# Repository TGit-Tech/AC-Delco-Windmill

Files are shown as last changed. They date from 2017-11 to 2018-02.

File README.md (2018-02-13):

# AC-Delco Alternator Windmill
An AC Delco alternator Windmill for wind power generation

Release 2017.12.10-beta ( Pictures Below )
*INCOMPLETE PROJECT - Use for experimental only*
Tested in 40mph winds found that gear slippage and destruction occurs
Need to Refactor the design for more stability
However, Project has demonstrated the ability to charge @ ~ 20mph winds
This includes self-excitement ( Actual power gained )

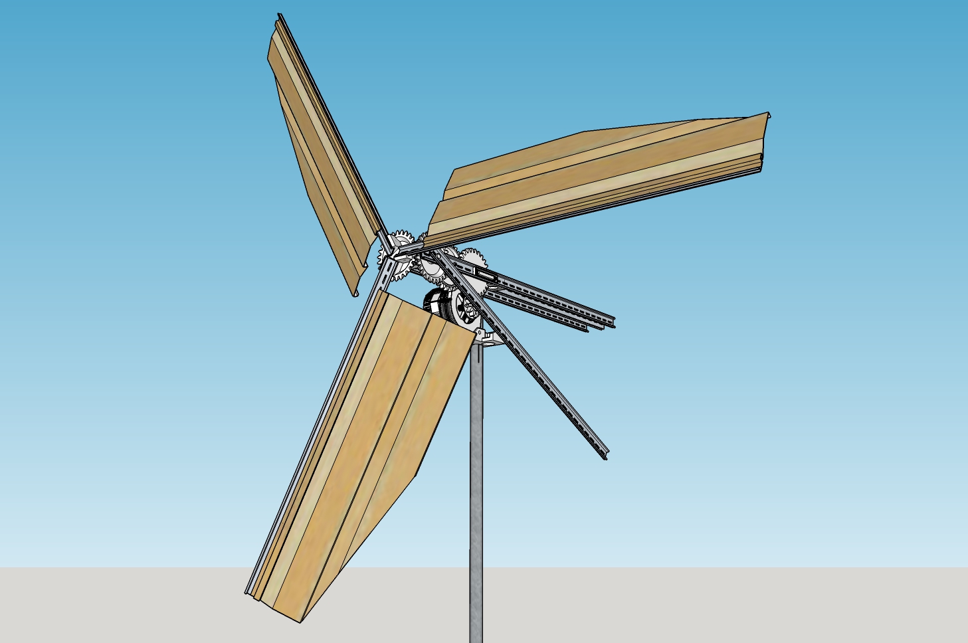
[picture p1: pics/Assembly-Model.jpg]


Current Work
*INCOMPLETE PROJECT - Use for experimental only*
Current Work still needs to be built and tested.  This is the 5-blade design
updated to handle high winds better by moving the alternator to behind the post
and creating a 5-Gear system in which the miter gears will transfer to straight
gears appropriately.  This also creates a 20:1 Ratio versus Version 2017.12.10-beta
 which created a 15:1 Ration.
 
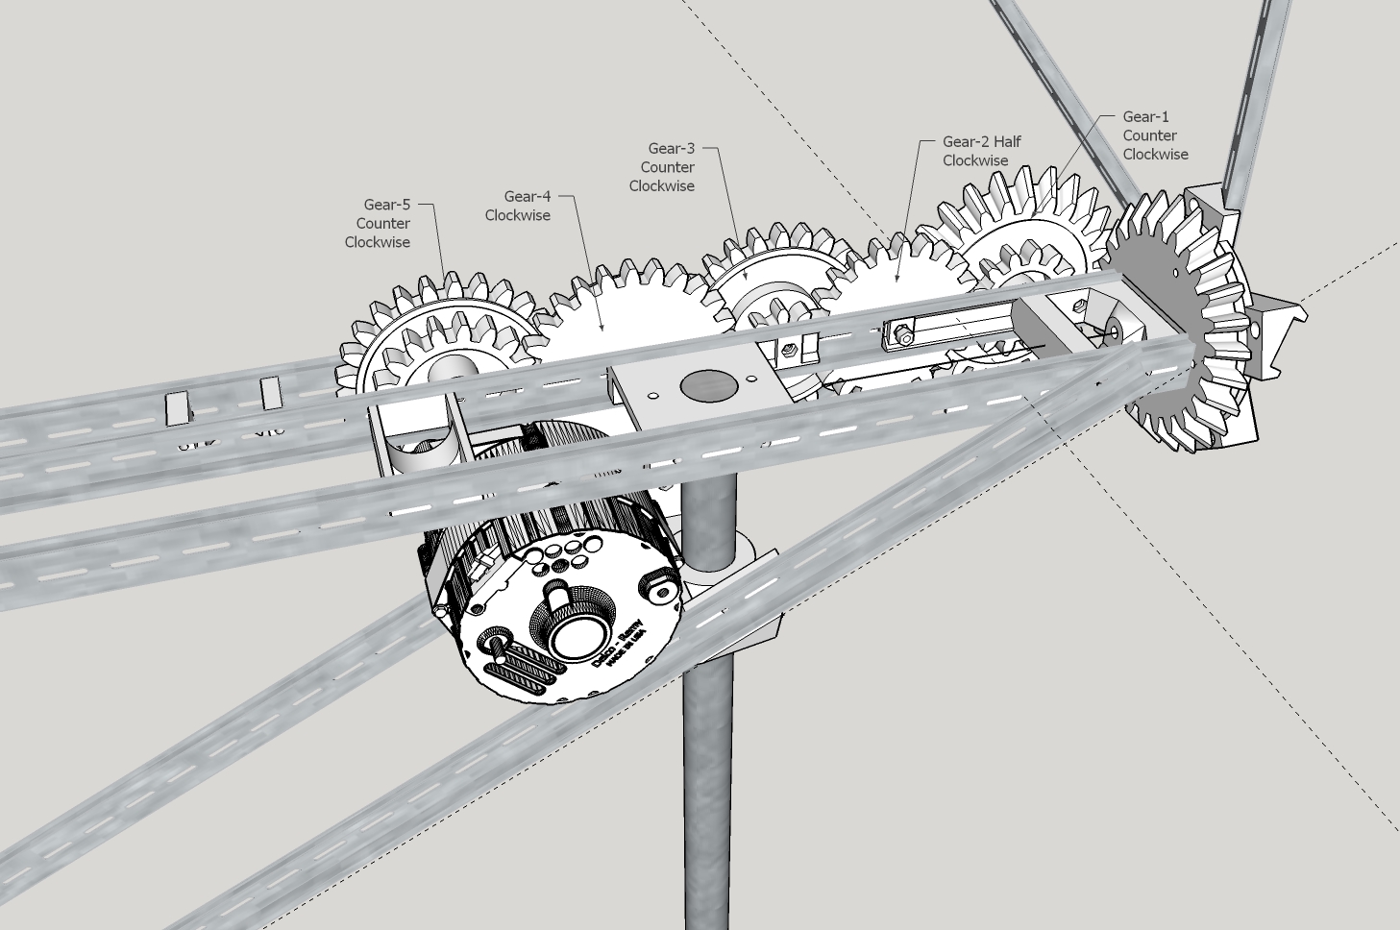
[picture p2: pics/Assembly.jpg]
Windmill


## Introduction
-
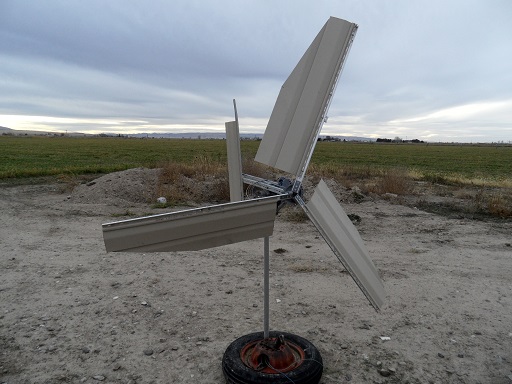
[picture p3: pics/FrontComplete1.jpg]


## Specification
- Takes 18-mph winds to barely start charging the battery
- Which doesn't take into account the ( 4V @ 0.85A = 3.4W ) Idle waste
- Can also run ( 3.7Vdc @ 0.62A = 2.294W )

## Alternator Excitement Regulation
In order to be efficient an Arduino ( Micro-controller ) must be used to adjust the alternators excitement level on the fly.  This was accomplished by designing a custom circuit detailed in the 'AltRegulator' folder.  The folder includes the Arduino Sketch last used to control excitement as well as KiCad design files.  The board was designed with the LinkSprite T8 CNC router using trace isolation. 

- Link to [http://www.linksprite.com/wiki/index.php5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]( CNC used. )

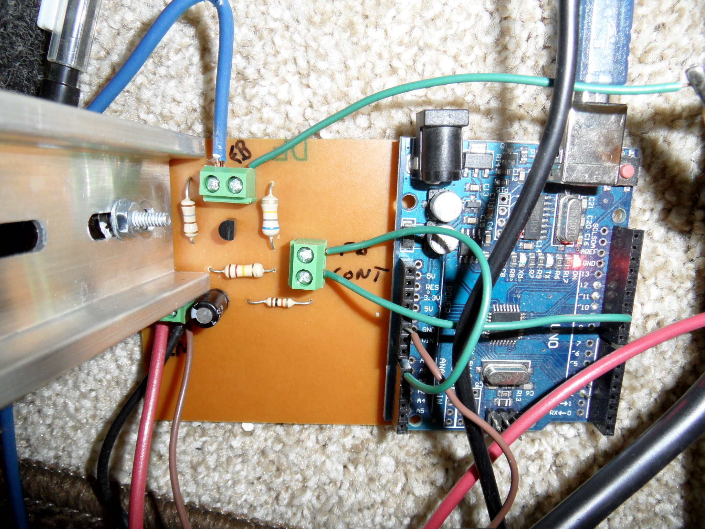
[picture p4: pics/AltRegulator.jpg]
Regulator-Circuit


## Raw Materials Needed
- (1) Free 12Vdc AC-Delco Auto Alternator [ $0 ]
- (10) DIN rail, slotted, 35mm, 10mm height, 1m length, aluminum [ $36.00 ]

    [https://www.automationdirect.com/adc/Shopping/Catalog/Enclosures_-z-_Subpanels_-z-_Thermal_Management_-z-_Lighting/Enclosure_Parts_-a-_Accessories/Internal_Component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)](https://www.automationdirect.com/adc/Shopping/Catalog/Enclosures_-z-_Subpanels_-z-_Thermal_Management_-z-_Lighting/Enclosure_Parts_-a-_Accessories/Internal_Component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)
    
- (1) Double 5" x 144" Beige Vinyl Lap Siding [ $7.95 ]
    
    [https://www.homedepot.com/p/Double-5-in-x-144-in-Beige-Vinyl-Lap-Siding-PC50NBH/302174965](https://www.homedepot.com/p/Double-5-in-x-144-in-Beige-Vinyl-Lap-Siding-PC50NBH/302174965)

## Electrical Materials
- 14 AWG Wire; Enough for Excitement ( pole 1 ) and Regulator ( pole 2 )
- 10 AWG Wire; Alternator ( Batt. ) to Batterry
- 40 Amp Diode?
- (2) Female Solderless Connectors for Alternator ( pole 1 & pole 2 )
- (2) O-Ring Solderless Connectors for Alternator ( Batt. & Ground )
- Incomplete list; check back later

## Bolts Needed
    - (1) 5/16" x 5" Coarse Bolt    Hub-Mount Cross Bolt
    - (1) 5/16" x 2" Bolt           For Hub Center
    - (2) 5/16" Nuts                For Double Nuts on Hub Bolt
    - (1) 5/16" x ?" Bolt           For Alternator Top Mount ( Alt Threaded Hole )
    - (1) 3/8" x ?" Bolt            For Alternator Bottom Mount
    - (1) 3/8" Nut                  For Alternator Bottom Mount
    - (4) #10-24 x 2" Screws        For 4-Rail Gears ( 9.1x Step Up )
    - (8) #10 Nuts                  For Double nuts on each Gear screw
    - (8) #10 x 3/4" Wide Washers   For each side of Rail Gears
    - (9) #10-24 x 1/2" Screws      For Vinyl Siding to DIN / 3-per-blade
    - (9) #10 Standard Washers      For Vinyl Siding to DIN / 3-per-blade
    - (9) #10 Nuts                  For Vinyl Siding to DIN / 3-per-blade
    
## Tools Needed
- Wrench Sizes
    - Phillips Head Screwdriver for #10 Screws
    - 3/8" for #10 Machine Screws
    - 1/2" for Hub, Alt Top Mount
    - 9/16" for Alt Bottom Mount
    - 15/16" for Alt Center Bolt
    
- Drill Bits
    - Drill bit for Top Alternator Bolt hole size 5/16" bolt

## Knowledge obtained
- Alternator excitement
    - Pole #1 closest to Batt. is Excitement Source
    - Pole #2 Turns ON/OFF Pole #1 Excitement at ~15Vdc and under
    - Pole #2 Isn't linear ( i.e. doesn't apply more excitement as voltage goes down )
    - Pole #1 @ 2.8Vdc,  0.35A = 0.98W but isn't strong enough to build voltage
    - Pole #1 @ 4.5Vdc,  1.24A = 5.58W is IDEAL for 9x gear-up
    - Pole #1 @ 10.7Vdc, 2.60A = 27.82W
    - Pole #1 @ 14.2Vdc, 3.50A = 49.7W
- Wiring
    - Use diodes to route alternator Batt. back into Pole #1 ( excitement )
    - Use diodes to ensure Batt. feeds battery only when charge levels
    - Startup feed of 4.5Vdc diode into Pole #1
    - Using above, when wind increases excitement increases till battery can charge
    - Need a Wind kick in start ( DC-DC Buck on battery w/Arduino turn on? )
    -

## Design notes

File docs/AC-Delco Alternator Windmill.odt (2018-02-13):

AC-Delco Remy Alternator Windmill

Written By: TGit-Tech (12/2017)

Feel free to use: no strings attached (text content only / images respectfully referenced)

# INTRODUCTION

## Specifications

- Gear Ratios

Name | Input | Output | Ratio | Rotation
Hub-Gear | Blades | 26 Outside Gears | 1:1 ( x1 ) | Clockwise
Gear-1 | 26 Outside Gears | 14 Inside Gears | 13:7 ( x0.5385 ) | Counter Clockwise
Gear-2 | 14 Inside Gears ( Gear-1 ) 22 Gears | 22 Gears 8 Gears ( Gear-3 ) | 4:7 ( x1.75 ) | Clockwise
Gear-3 | 8 Inside Gears | 26 Outside Gears | 4:13 ( x3.25 ) | Counter Clockwise
Gear-4 | 13 Inside Gears | 26 Outside Gears | 1:2 ( x2 ) | Clockwise
Gear-5 | 18 Inside Gears | 26 Outside Gears | 9:13 ( x1.44 ) | Counter Clockwise
Gear-6 Alternator | 26 Outside Gears ( Gear-5 ) | 11 Alternator Gears | 26:11 ( x2.36 ) | Clockwise

  - Total Ratio = Gear-Up x 20.8152

# Materials ( $205.11 )

## Hardware Materials ( $51.90 )

- (2) Double 5” Vinyl Lap Siding [ $7.95 @ 12-feet ]
  - Purchase @ https://www.homedepot.com/p/Double-5-in-x-144-in-Beige-Vinyl-Lap-Siding-PC50NBH/302174965
- (10) Aluminum DIN Rails - 35mm x 10mm x 1M, slotted [ $36/10-pack ]
  - Purchase @ https://www.automationdirect.com/adc/Shopping/Catalog/Enclosures_-z-_Subpanels_-z-_Thermal_Management_-z-_Lighting/Enclosure_Parts_-a-_Accessories/Internal_Component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
- 1” EMT Conduit Pipe sold @ 10-feet [ $7.25 @ 10-feet ]
  - Purchase @ https://www.homedepot.com/p/1-in-EMT-Conduit-101568/100400409
  - 1-3/16” (1.1875”) inside diameter measured
  - 1-4.5/16” (1.2813”) outside diameter measured
  - See https://creativeshelters.com/fittings/diameter

## Fasteners

- (18) #10-24 x 1” Machine Screws & Lock Nuts
  - (15) Blades to Hub ( 3x per Blade-to-Hub with 5-blades )
  - (3) Hub to Hub-Gear
- (15) #10-24 x 1/2” Machine Screws & Wide #10x3/4” Flat Washers & Lock Nuts
  - (3) Per Vinyl-to-DIN x (5) Blades

## Power Materials ( $112.43 )

- (3) 6Vdc Lead Acid Batteries [ $8.64/ea = $25.92 ]
  - https://www.walmart.com/ip/American-Hunter-DE645DC-6V-4-5A-HR-Rechargeable-Battery/40369551
- Solar Inverter 10.8Vdc to 30Vdc Grid Tie [ $86.51 ]
  - https://www.aliexpress.com/item/500w-on-grid-tie-solar-power-inverter-12v-24v-input-dc-to-home-voltage-220v-110v/32822544294.html

## 3D-PLA Filament ( $40.78 )

- 3D Printed Parts ( Prices are based on $14.99 per 1Kg Spool of PLA )
  - Drive Train – Front to Back ( $27.54 )
    - Hub = 260 grams = $4.87 = (3) #10-24 x 1” Bolts & Nuts
    - Hub-Gear = 209 grams = $3.92 = (1) 5/16” x ? Bolt & (2)Nuts
    - Gear-1 = 256 Grams = $4.80 = (1) #10-24 x 2” Bolt & (2)Nuts & (2)5/16” Flat Washers
    - Gear-2 = 69 Grams = $1.29 = (1) #10-24 x 2” Bolt & (4)Nuts & (2)5/16” Flat Washers
    - Gear-3 = 152 Grams = $2.85 = (1) #10-24 x 2” Bolt & (2)Nuts & (2)5/16” Flat Washers
    - Gear-4 = 202 Grams = $3.79 = (1) #10-24 x 2” Bolt & (2)Nuts & (2)5/16” Flat Washers
    - Gear-5 = 232 Grams = $4.35 = (1) #10-24 x 2” Bolt & (2)Nuts & (2)5/16” Flat Washers
    - Gear-6 ( Alternator ) = 86 Grams = $1.61 = Pulley Nut and Washer that comes with Alternator
  - Center Pieces – Front to back ( $6.90 )
    - Hub-Mount-26g = 160 Grams = $3.00 = (2)#10-24 x 3/4” Bolts & Lock-Nuts, (1)5/16” x 6” Bolt & (2)Nuts
    - Post-Mount = 140 Grams = $2.55 = (2)#10-24 x 3/4” Bolts & Nuts
    - Alt-UpperMount = 69 Grams = $1.35 = (1)#10-24 x 3/4” Bolts & Nuts
  - Other Pieces ( $ 6.34 )
    - Alt-LowerMount = 257 Grams = $4.78 = (2)#10-24 x 3/4” Bolts & Lock-Nuts
    - (5) Blade-NutHolders = 83 Grams ( 17/ea ) = $1.56 = (10)#10-24 x ? Bolts & Nuts & Lock-Nuts
    - Bolt-Drill-Guide
    - DIN Clamp = 21 Grams = $0.39 = (2)#10-24 x 2” Bolts & Lock-Nuts

# Assembly Instructions

## Frame

1. Connect (2) DIN Rails together with Post-Mount.stl
  a. Insert #10 Nuts into the side slots of the Post-Mount ( may require pounding in with a hammer and punch )
  b. Position Post-Mount between 2-DIN Rails centered around Slot #10 of both rails
    - One side-hole at Slot #9
    - One side-hole at Slot #11
  c. Insert (2) #10-24 x 3/4” machine screws on Non-Gear Side
2. Install Gear-2 and Gear-2-Standoff
- Attach (2) DIN Rails to the Post-Mount.stl
  - Install #10 Nuts into the Post-Mount
  - Center Post-Mount around Din Rail Slot # 10
  - Align first screw hole in DIN Rail Slot #9
  - Align second screw hole in DIN Rail Slot #11
  - (2) #10-24 x 3/4” machine screws & nuts
- Insert Nut in Hub-Mount
  - Insert Nut in Hub-Mount
  - Drive in (2) #10-24 x 3/4” machine screws & nuts in very back of 1st slot into Hub-Mount
  - Align second DIN ( Gear DIN ) to Hub-Mount on the right? side
  - Drill through both DIN rails where 5/16” bolt will go
  - Turn Over
  - Drill through the DIN rail so 5/16” bolt can come through other side
  - Insert 5/16” Bolt
- Setup Brace DIN
  - Drill out back of the 1st slot for 5/16” Bolt
- Install first Gear
  - Insert 5/16” x 5” bolt through Brace DIN, Gear DIN
  - Through Washer
  - Through Gear-1
  - Through Gear-1-Spacer
  - Through Hub-Mount
- Install Second Gear FIRST
  - This allows the Hole for the 1st Gear to be drilled correctly

## Blades

- Cut Vinyl Siding
  - Cut Vinyl Siding into (5) 32” long sections
- Attach Vinyl Siding Sections to DIN Rails
  - Attach Each 32”-Vinyl Siding Section to a DIN Rail with (3)#10-1/2” + #10x3/4” Washer + Lock Nut
  - Be sure the Vinyl Siding is attached so the DIN Rail will mount to the Hub with the DIN Rail out front and the Siding angled backwards
- Attach Blades to Hub
  - Using a Blade-NutHolder for each Blade; attach each blade to the Hub with (3)#10-1” Machine Screw + Lock Nut

# Lessons Learned

## Why the 5/16” x 6” Bolt across the front?

Original designs showed the pressure from the hub driving the 90-degree angle produced more force than the outer DIN-Rail could handle effectively. The only vertical alignment support available is either behind all gears and the small #10 machine screws that goes through each gear. Since the #10 screws through the gears cannot be tightened due to gear clamping and there is no way to brace the outer DIN at the front and back. The long 5/16” Bolt keeps all front size DINs in vertical alignment while significant force is applied on the Miter gear.

## Why a 2-piece Hub?

First; There is no way to print the overhang required to keep the miter-gear tooth overlap from hitting the Blade slot supports. Thus the gap ( lifted hub ) is created using a Hub and Hub-Gear piece bolted together.

Second; Even if a model could be designed to address the miter-gear tooth overlap – The two piece design contains a hallow center and thus saves a substantial amount of plastic resources.

## Why the idle-gear design on 5-blade revision?

The most recent 3-blade design worked well in 40mph winds most of 5 or 6 hours. However; the design started to snap under heavy load and started to come apart first by slippage on the miter-gears ( Hub 90-angle ) in which there was miter-to-miter tooth skipping as well as 1st Gear to miter tooth skipping. The 5-blade design carries not only a better ( larger and tighter ) miter-gear connection by overlapping the miter-teeth but also introduced the idler-gear to eliminate the 1st Gear to angled miter gear which was also causing tooth skipping problems.

## Why 5-Gears instead of 3?

One reason for the 5-Gear was spacing for the new idler gear introduced in the 4.3 issue described above.

However, most importantly, the 5-Gear system was a result of getting the alternator back behind the post while allowing for exactly the 10” of blade clearance on the front. The goal was to have the smallest front over-hang as possible ( for support purposes ) that gave enough clearance to guarantee the blades never made contact with the post or a front mounted alternator ( which also caused blade-binding issues on previous designs ).

Allowing the maximum 10” clearance on the front for the blades required moving the alternator behind the post and thus required 5-Standard size gears to move the driving mechanism back. A belt or chain design was considered but to limit costs and possibly even enhance charging ability at a 20:1 ratio; the extra gearing was included.

( 3.2 Assembly Instructions :: Blades :: Blades ) Page -4-

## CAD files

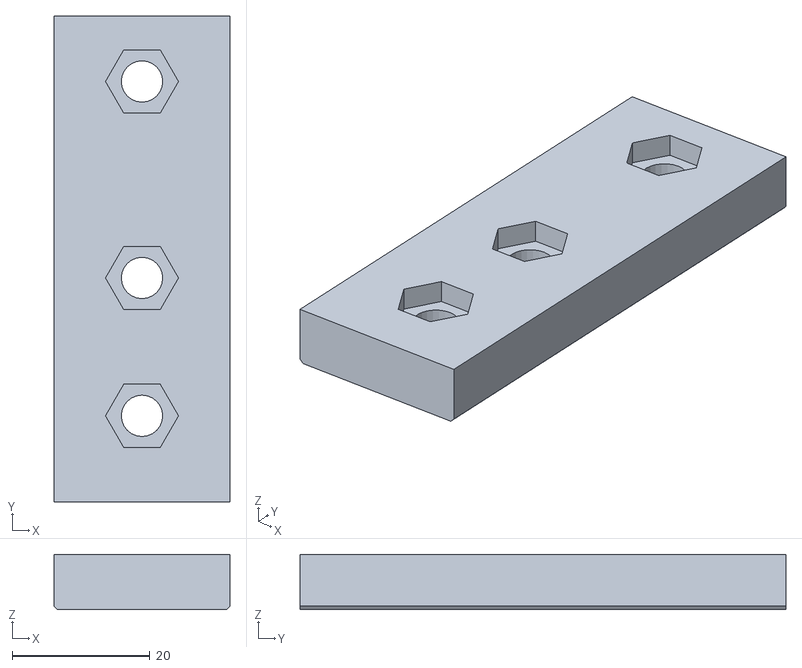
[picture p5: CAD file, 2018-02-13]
3D-Prints-STL/Blade-NutHolder.stl
25.5 x 70.5 x 8.00

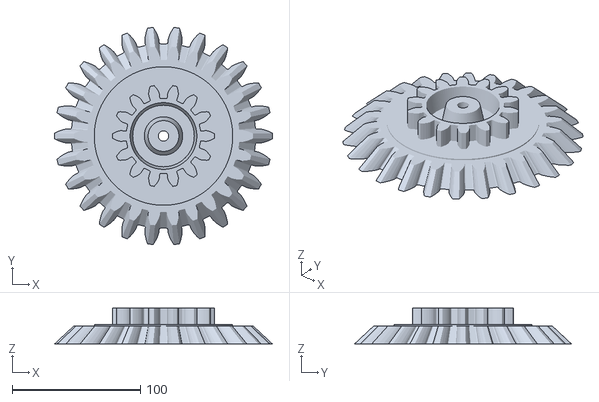
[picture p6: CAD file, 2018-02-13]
3D-Prints-STL/Gear-1.stl
170.0 x 169.3 x 28.0

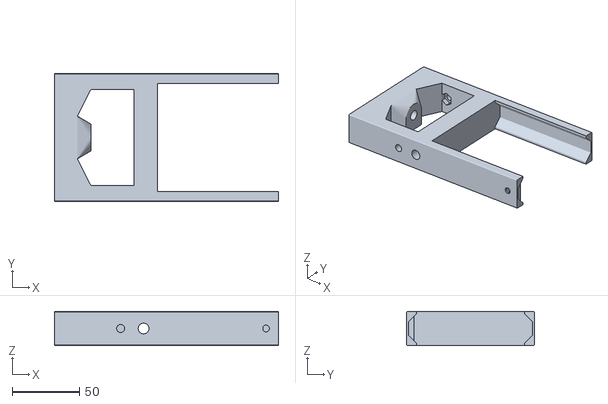
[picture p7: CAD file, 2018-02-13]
3D-Prints-STL/Hub-Mount-26g.stl
166.3 x 95.0 x 25.5

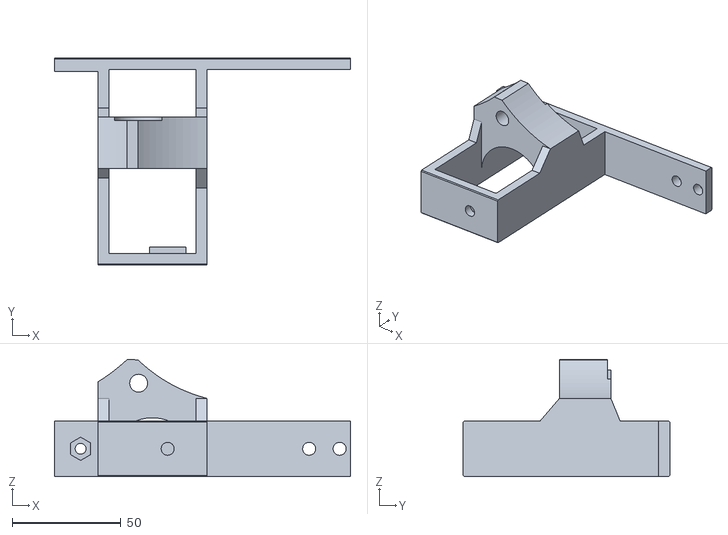
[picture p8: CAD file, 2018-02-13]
3D-Prints-STL/Alt-UpperMount.stl
136.0 x 95.0 x 53.8

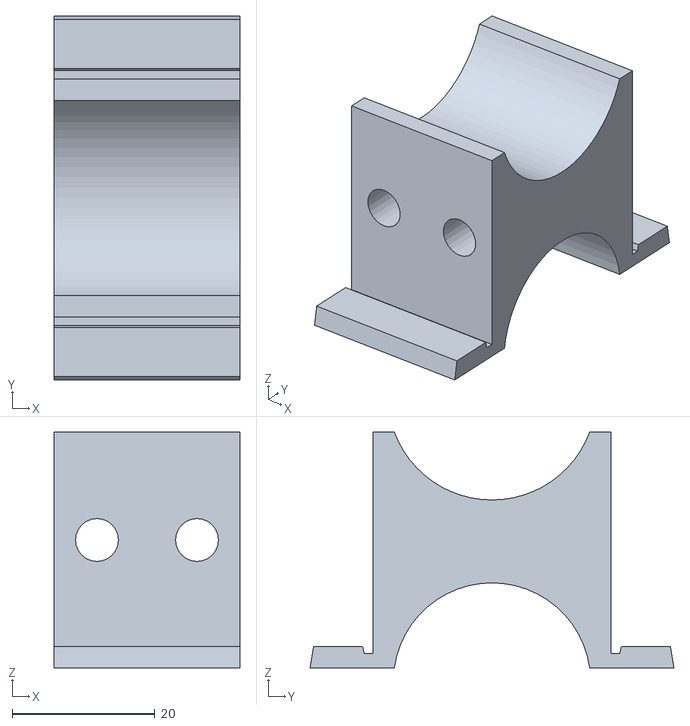
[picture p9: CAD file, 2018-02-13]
3D-Prints-STL/DIN-Clamp.stl
26.0 x 50.9 x 33.0

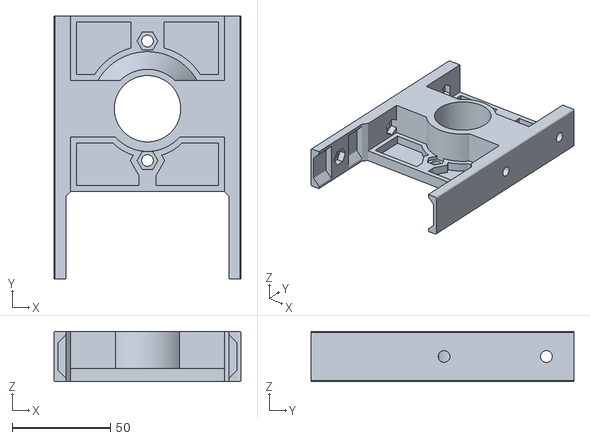
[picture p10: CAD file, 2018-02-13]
3D-Prints-STL/Post-Mount.stl
95.0 x 133.6 x 25.5

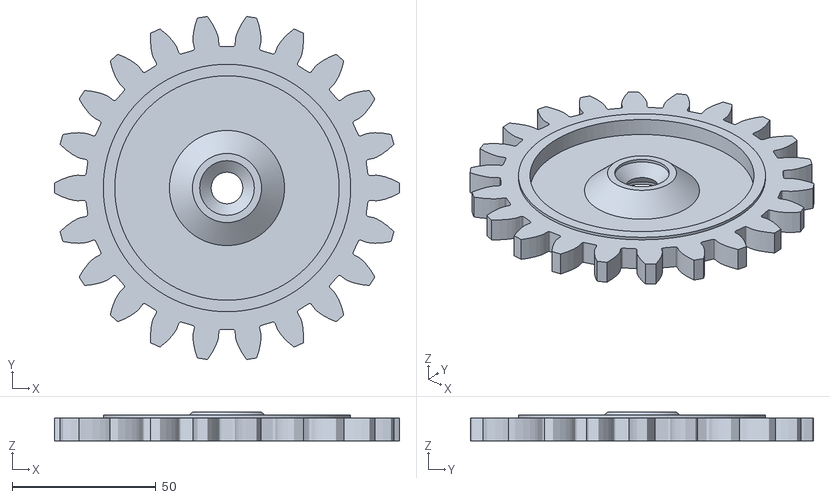
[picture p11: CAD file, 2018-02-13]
3D-Prints-STL/Gear-2-half-v3.stl
119.9 x 119.2 x 10.0

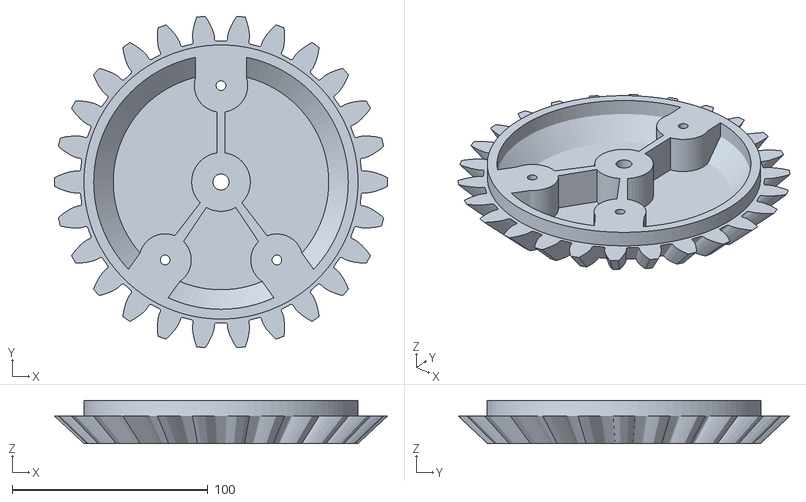
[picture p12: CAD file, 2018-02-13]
3D-Prints-STL/Hub-Gear.stl
170.0 x 169.3 x 22.0

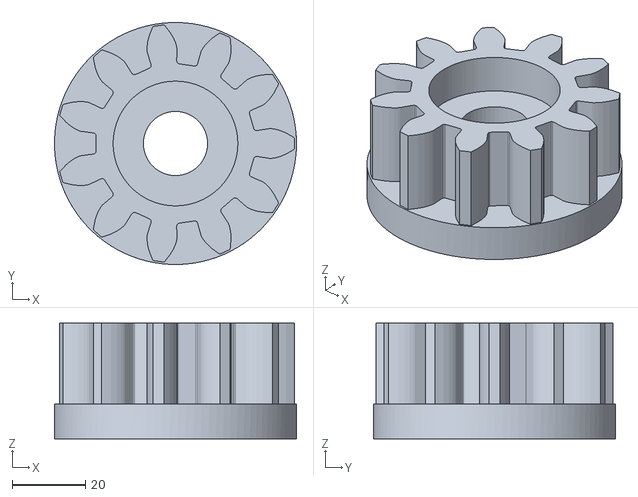
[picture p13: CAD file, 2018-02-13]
3D-Prints-STL/Gear-6-Alternator.stl
66.0 x 66.0 x 31.5

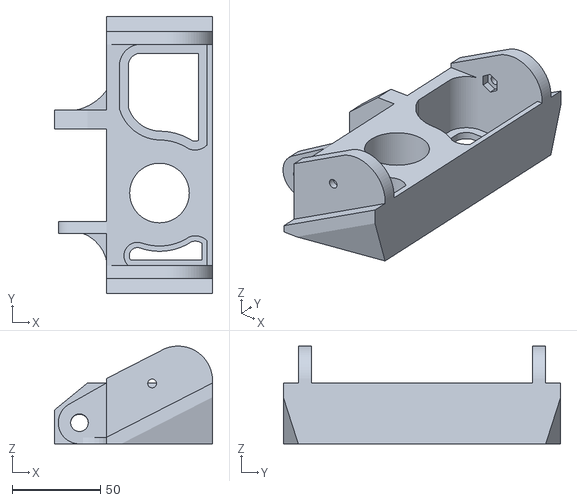
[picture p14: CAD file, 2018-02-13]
3D-Prints-STL/Alt-LowerMount.stl
89.4 x 157.0 x 55.4

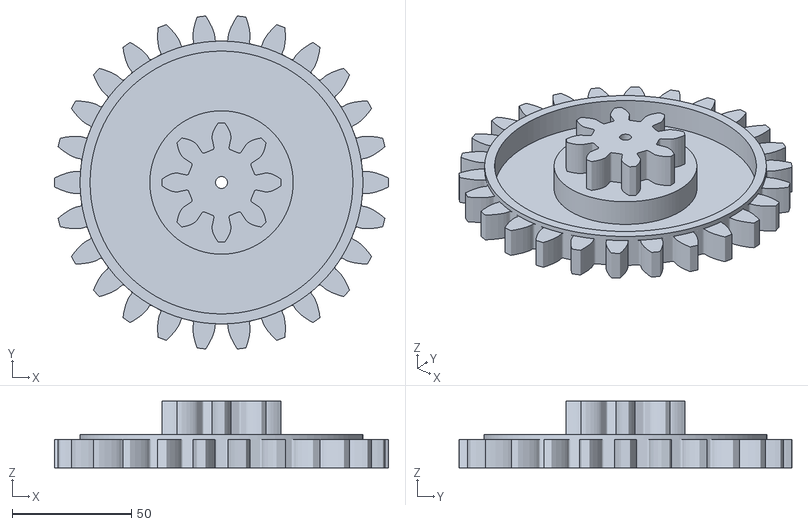
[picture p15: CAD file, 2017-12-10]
3D-Prints-STL/Gear-3-3_25x.stl
140.0 x 139.4 x 28.0

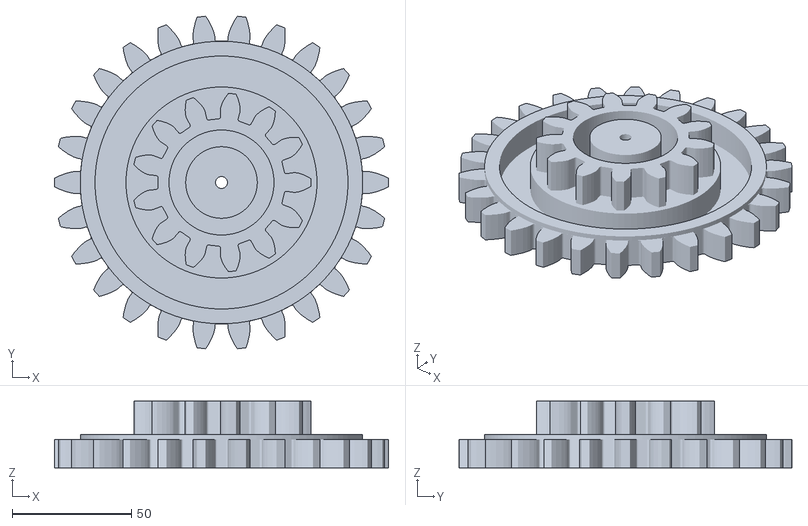
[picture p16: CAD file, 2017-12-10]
3D-Prints-STL/Gear-4-2x.stl
140.0 x 139.4 x 28.0

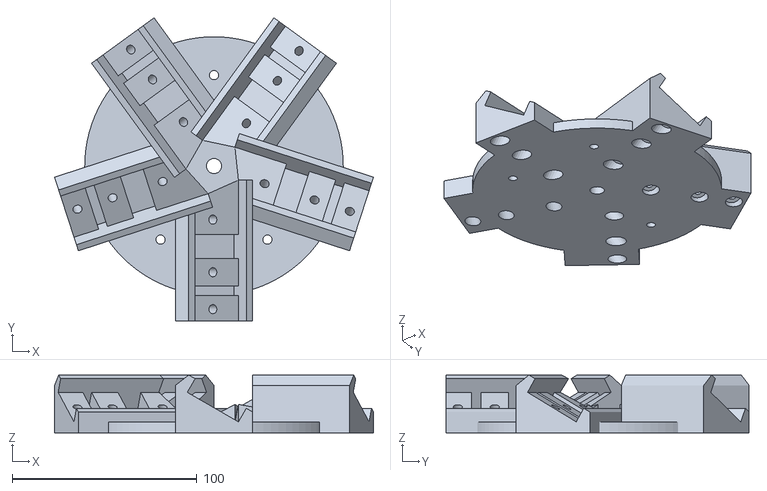
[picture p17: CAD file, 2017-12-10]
3D-Prints-STL/Hub.stl
172.7 x 164.3 x 31.4

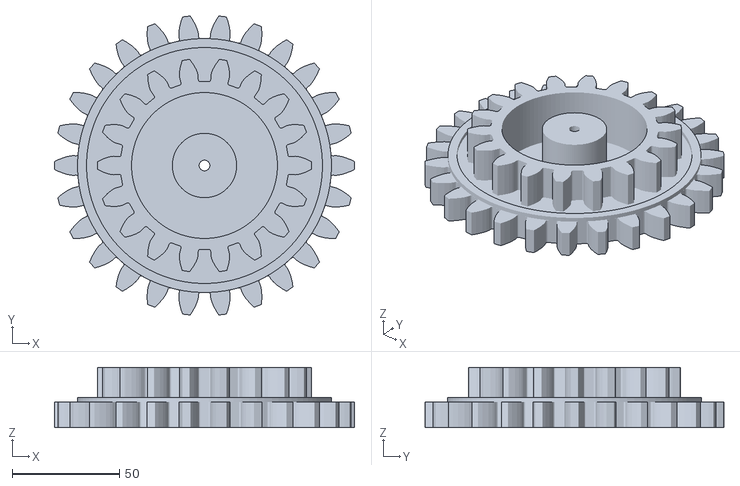
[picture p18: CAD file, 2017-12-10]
3D-Prints-STL/Gear-5_1_4x.stl
140.0 x 139.4 x 28.0

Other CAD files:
3D-Prints-STL/Alt-Fan.stl
3D-Prints-STL/Post-Clamp.stl
3D-Prints-STL/Bolt-Drill-Guide.stl
3D-Prints-STL/Gear-2-half-v2.stl
3D-Prints-STL/Gear-2-half.stl
3D-Prints-SketchUp/Alt-Fan.skp
3D-Prints-SketchUp/Alt-LowerMount.skp
3D-Prints-SketchUp/Alt-UpperMount.skp
3D-Prints-SketchUp/Blade-NutHolder.skp
3D-Prints-SketchUp/Bolt-Drill-Guide.skp
3D-Prints-SketchUp/DIN-Clamp.skp
3D-Prints-SketchUp/Gear-1.skp
3D-Prints-SketchUp/Gear-2-half-v2.skp
3D-Prints-SketchUp/Gear-2-half-v3.skp
3D-Prints-SketchUp/Gear-2-half.skp
3D-Prints-SketchUp/Gear-3-3_25x.skp
3D-Prints-SketchUp/Gear-4-2x.skp
3D-Prints-SketchUp/Gear-4-Spacer.skp
3D-Prints-SketchUp/Gear-5_1_4x.skp
3D-Prints-SketchUp/Gear-6-Alternator.skp
3D-Prints-SketchUp/Hub-Gear.skp
3D-Prints-SketchUp/Hub-Mount-26g.skp
3D-Prints-SketchUp/Hub.skp
3D-Prints-SketchUp/Post-Clamp.skp
3D-Prints-SketchUp/Post-Mount.skp
Design-Files/Gears-Flat.skp
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

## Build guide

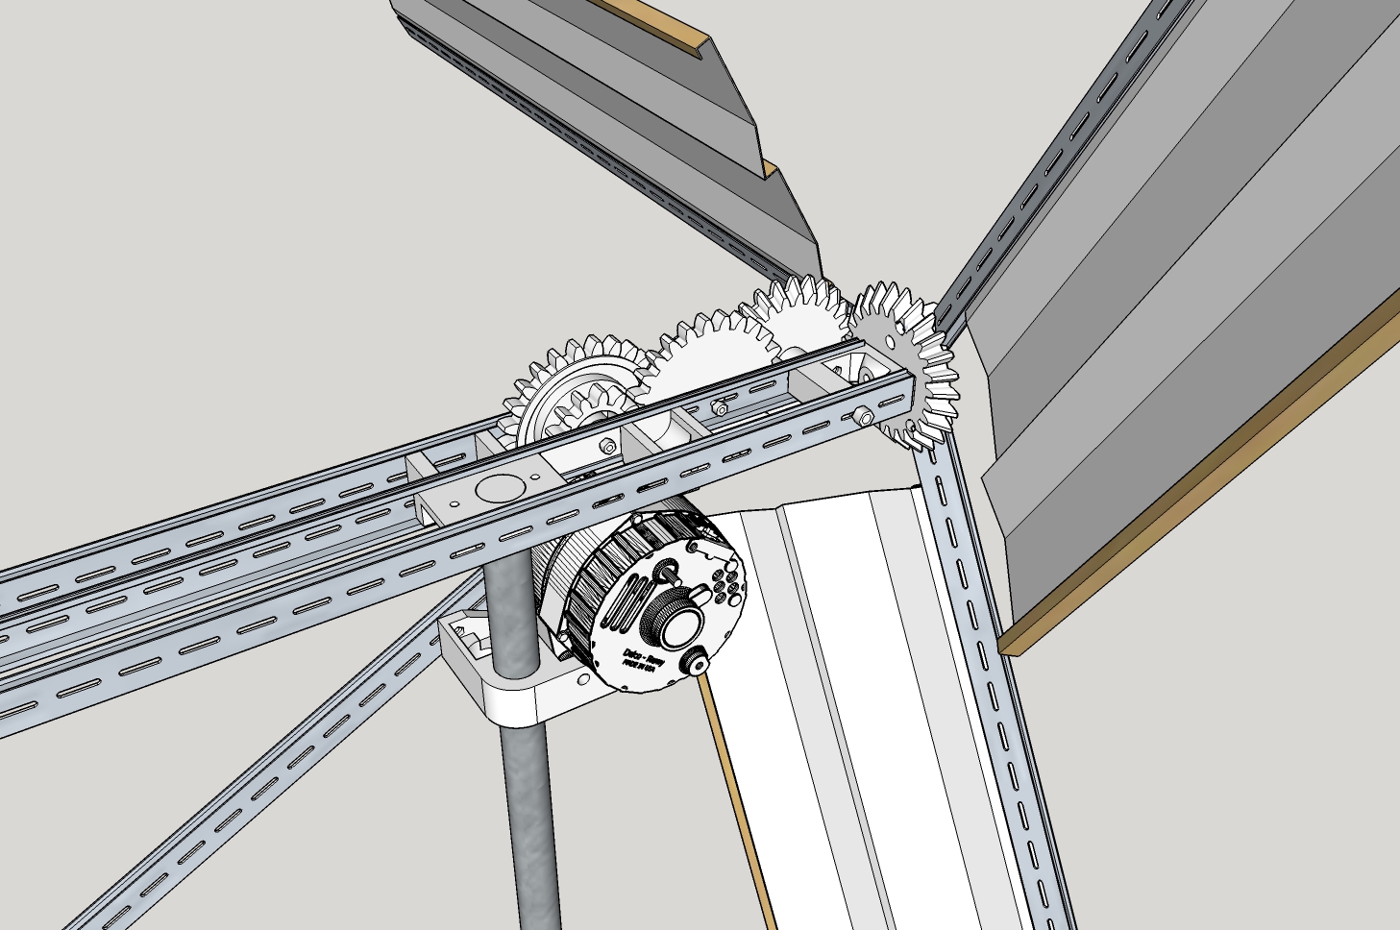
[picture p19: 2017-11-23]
pics/Assembly-RightSide.jpg

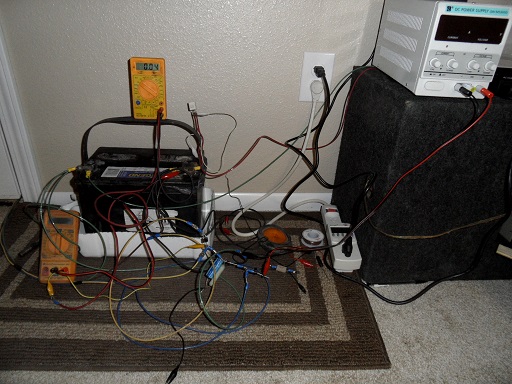
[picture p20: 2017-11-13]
pics/BatteryNWiring.jpg

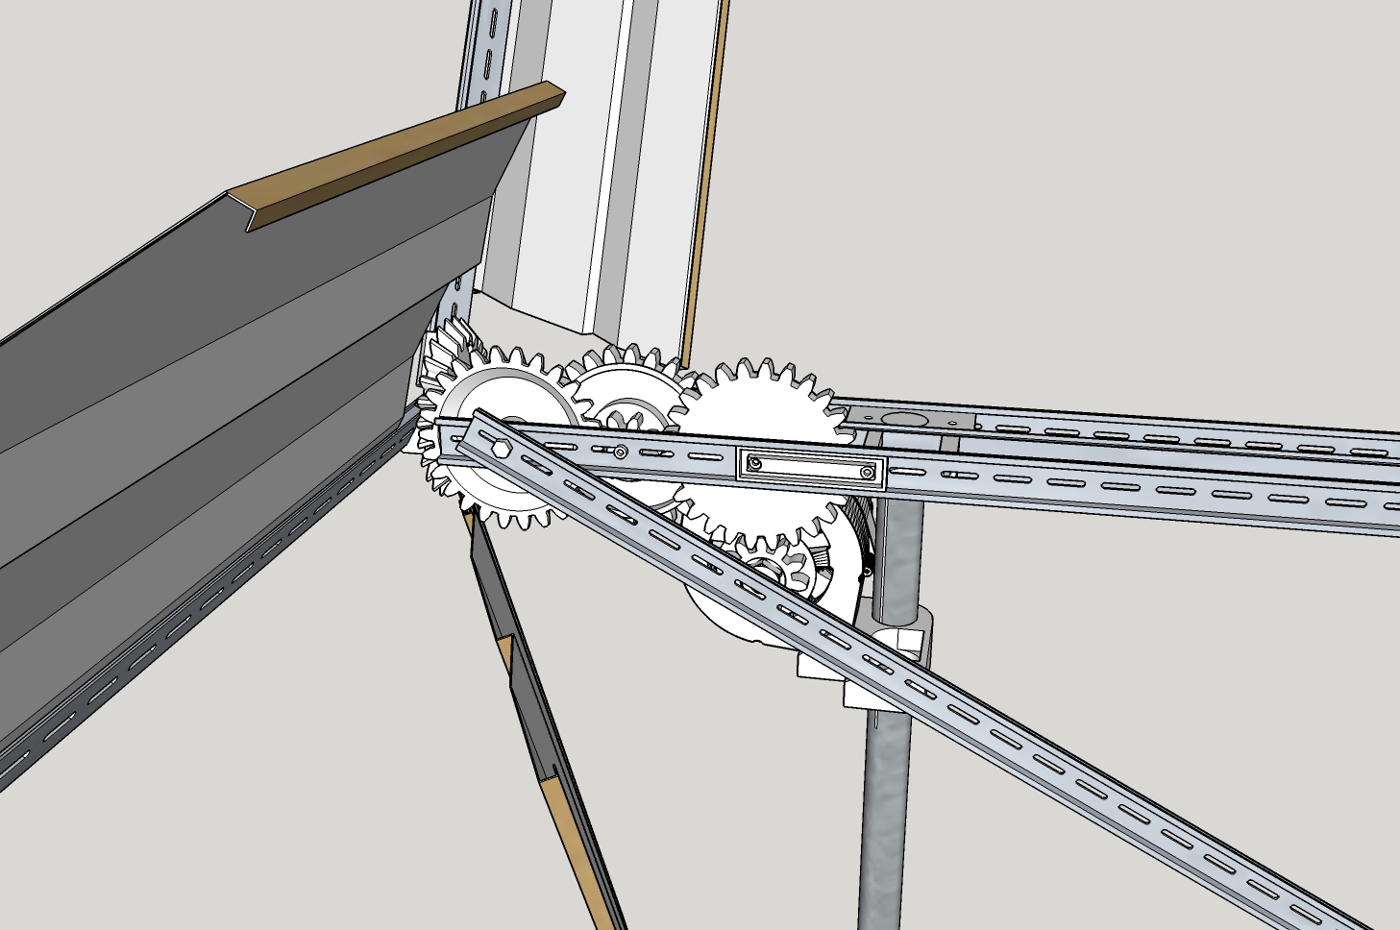
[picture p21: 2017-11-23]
pics/Assembly-LeftSide.jpg

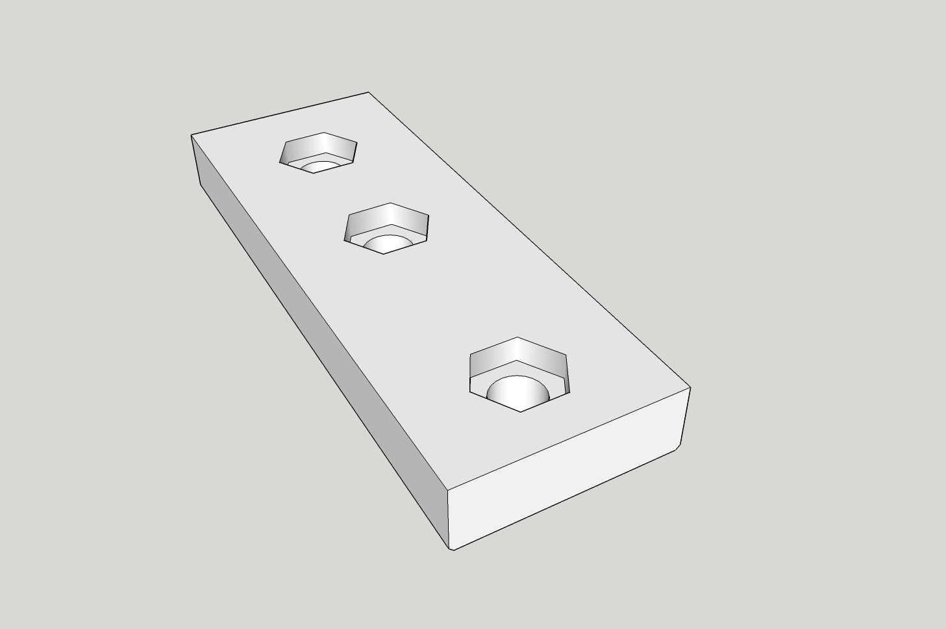
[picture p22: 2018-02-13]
3D-Prints-JPG/Blade-NutHolder.jpg

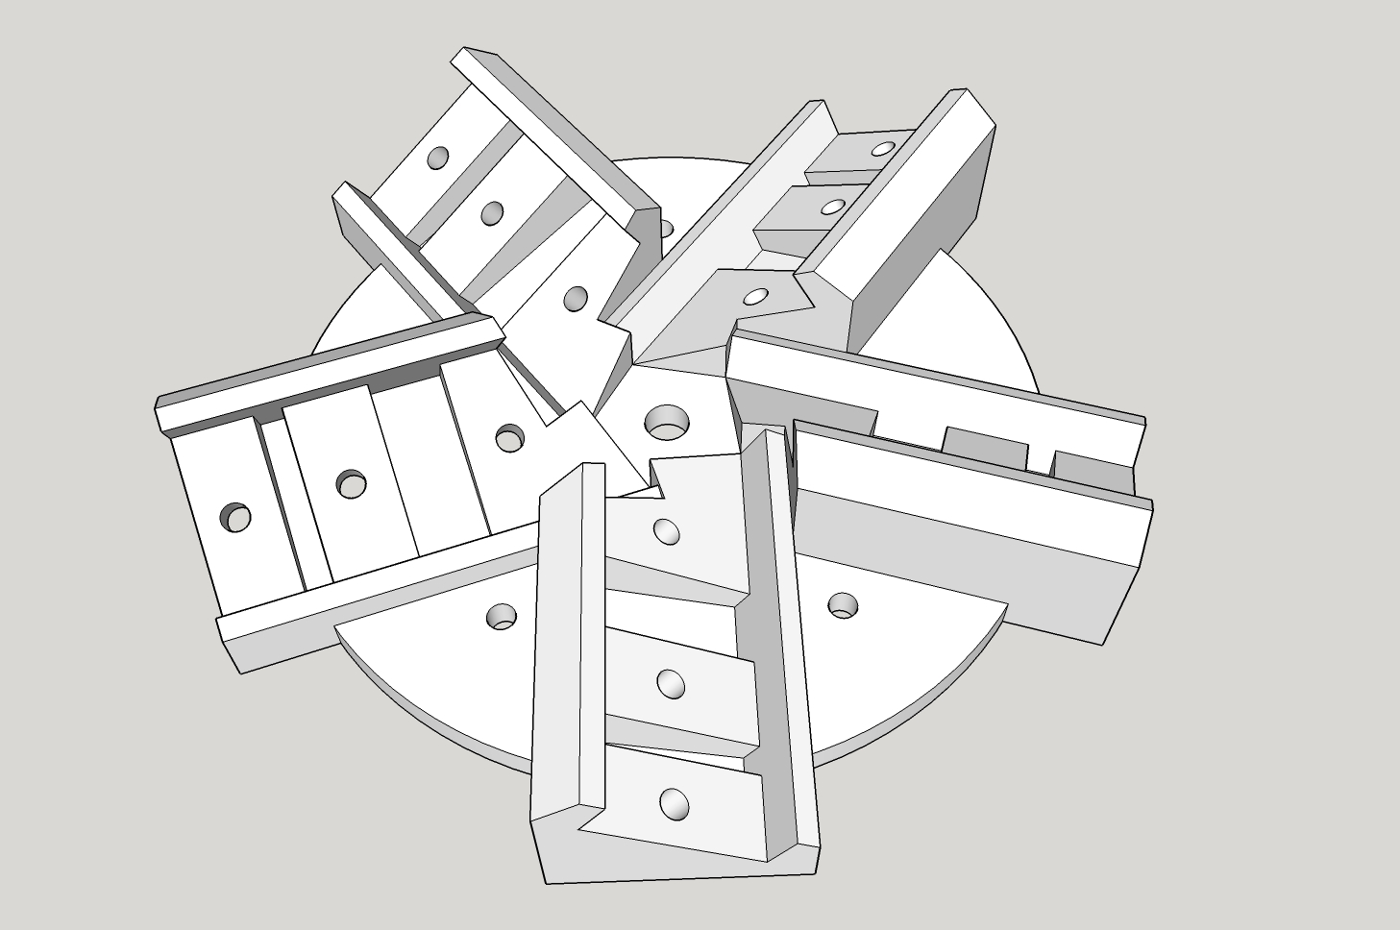
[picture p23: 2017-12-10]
3D-Prints-JPG/Hub.jpg

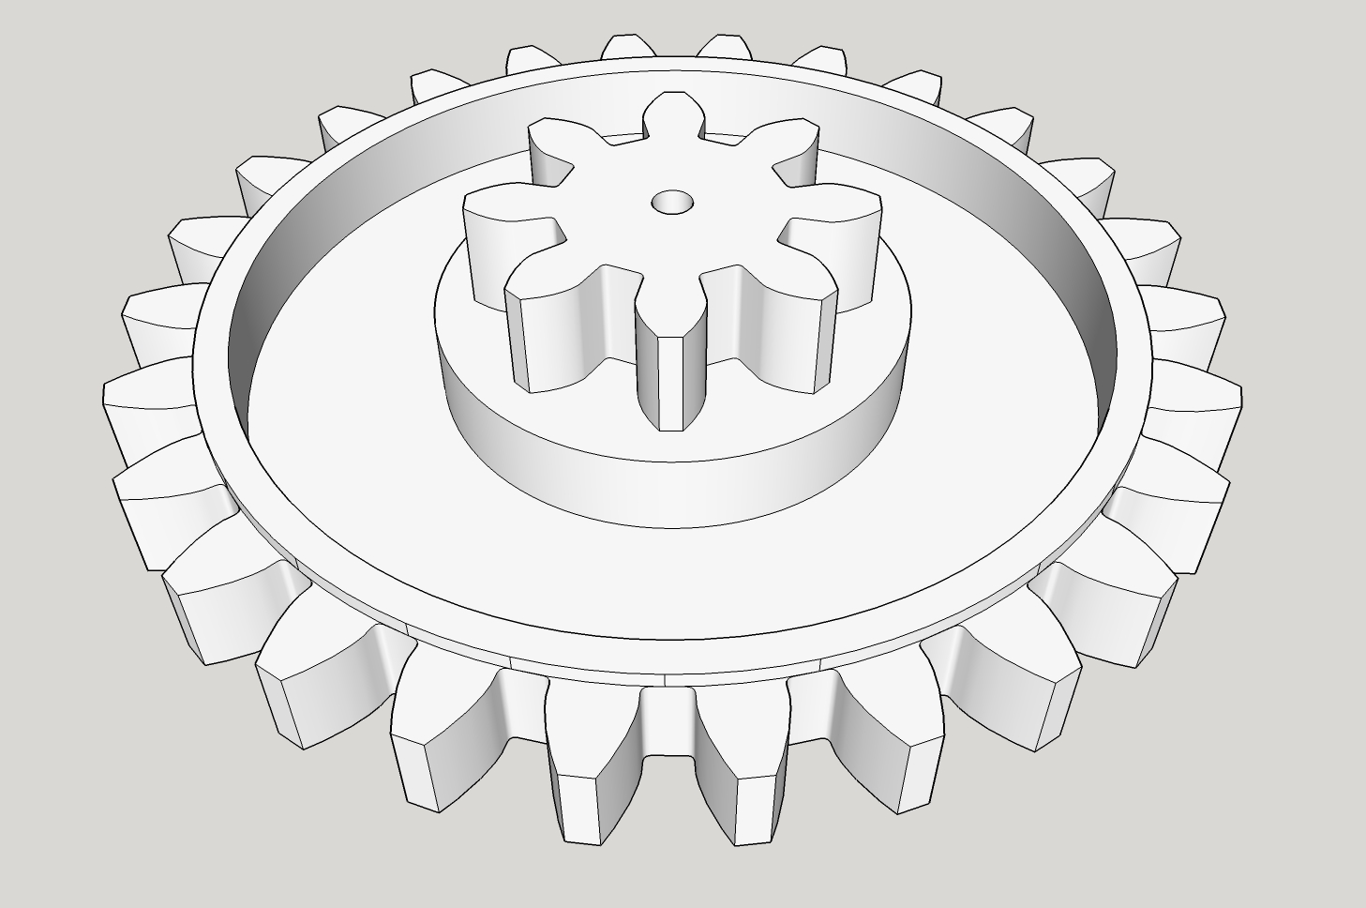
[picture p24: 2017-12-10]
3D-Prints-JPG/Gear-3-3_25x.jpg

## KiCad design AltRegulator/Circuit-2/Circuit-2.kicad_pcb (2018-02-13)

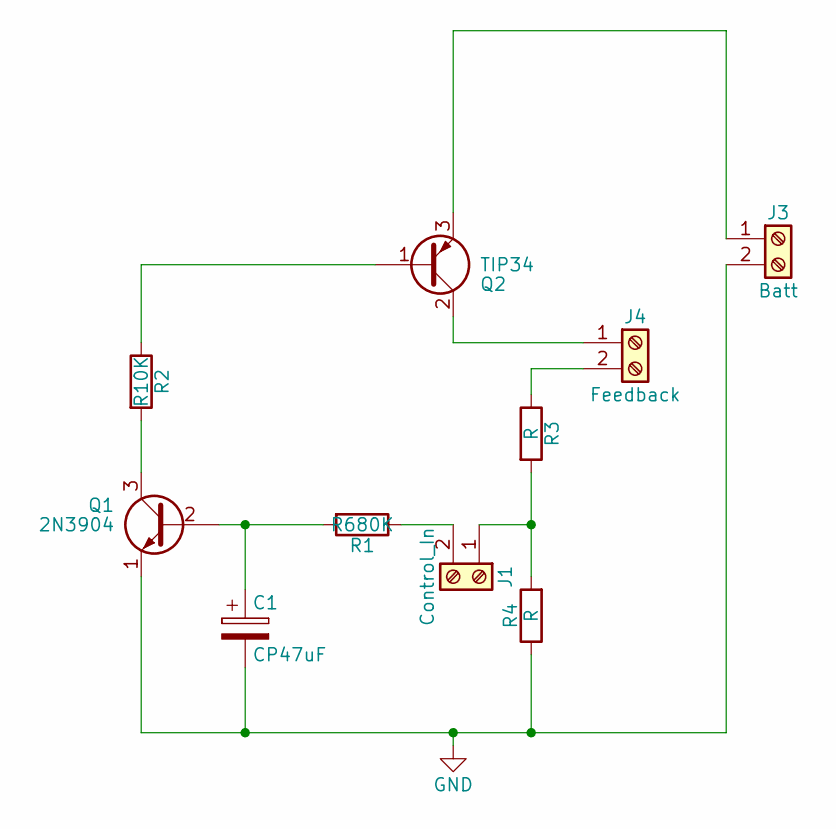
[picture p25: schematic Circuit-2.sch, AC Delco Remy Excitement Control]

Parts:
C1: CP47uF; CP_Radial_D5.0mm_P2.50mm
J1: Control_In; TerminalBlock_bornier-2_P5.08mm
J3: Batt; TerminalBlock_bornier-2_P5.08mm
J4: Feedback; TerminalBlock_bornier-2_P5.08mm
Q1: 2N3904; TO-92_Molded_Narrow
Q2: TIP34; TO-247_TO-3P_Vertical
R1: R680K; R_Axial_DIN0414_L11.9mm_D4.5mm_P15.24mm_Horizontal
R2: R10K; R_Axial_DIN0414_L11.9mm_D4.5mm_P15.24mm_Horizontal
R3, R4: R; R_Axial_DIN0414_L11.9mm_D4.5mm_P15.24mm_Horizontal

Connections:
GND: C1.2, J3.2, Q1.1 (E), R4.1
unnamed: C1.1, Q1.2 (B), R1.2
unnamed: J1.1, R3.2, R4.2
unnamed: J1.2, R1.1
unnamed: J3.1, Q2.3 (E)
unnamed: J4.1, Q2.2 (C)
unnamed: J4.2, R3.1
unnamed: Q1.3 (C), R2.2
unnamed: Q2.1 (B), R2.1

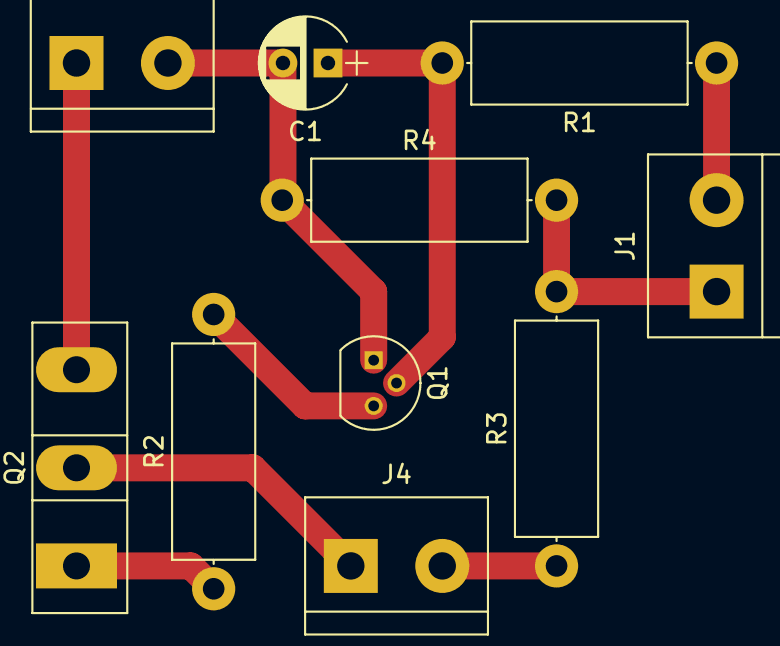
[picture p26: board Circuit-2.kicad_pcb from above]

Board: 2 copper layers, 10 parts (0 on the bottom side), 9 nets.

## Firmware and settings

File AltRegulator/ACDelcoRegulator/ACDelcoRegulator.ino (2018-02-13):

#define TEST_INTERVAL 1000
#define TEST_INTERVAL_MAX 15000
#define EXCITEMENT_DELAY 1000

unsigned long NowTime = 0;
unsigned long LastTime = 0;
unsigned long IdleCount = 0;
unsigned long TestInterval = TEST_INTERVAL; // Starting interval will self-adjust
int Excite = 0;
float IN = 0.0;
float OUT = 0.0;
float EFFICENT = 0.0;
bool Show = false;

void Excitement(int Value) {
  analogWrite(10,Value);
  analogWrite(11,Value);
}

void setup() {
  // put your setup code here, to run once:
  pinMode(A0,INPUT);
  Serial.begin(9600);
}

void loop() {
  // put your main code here, to run repeatedly
  IN = Excite/15.0;
  OUT = analogRead(A0)/30.0;
  EFFICENT = OUT/IN;
  
  // Timed Events
  NowTime = millis();
  if ( NowTime > (LastTime + TestInterval) ) {
    LastTime = millis();
    Show = true;
  }

  if ( Excite > 100 ) {
    if ( Show ) Serial.print("99-");
    if ( EFFICENT > 0.85 ) Excite = Excite + 10;
    if ( EFFICENT < 0.75 ) Excite = Excite - 10;
  } else if ( Excite > 61 ) {
    if ( Show ) Serial.print("60-");
    if ( EFFICENT > 0.75 ) Excite = Excite + 10;
    if ( EFFICENT < 0.65 ) Excite = Excite - 10;
  } else if ( Excite > 41 ) {
    if ( Show ) Serial.print("40-");
    if ( EFFICENT > 0.60 ) Excite = Excite + 10;
    if ( EFFICENT < 0.50 ) Excite = Excite - 10;
  } else {
    if ( Show ) Serial.print("00-");
    if ( EFFICENT > 0.02 ) { Excite = Excite + 10; }
    else { Excite = Excite - 10; }
  }

  if ( Show ) {
    Serial.print("IN->");Serial.print(IN);Serial.print("\t");
    Serial.print("OUT->");Serial.print(OUT);Serial.print("\t");
    Serial.print("EFF->");Serial.println(EFFICENT);
    Show = false;
  }
  // 26 will induce some at high winds
  if ( Excite < 28 ) Excite = 28;
  if ( Excite > 255 ) Excite = 255;
  Excitement(Excite);
  // Test for activity ( PS @ 12.5Vdc )
  // 50 = 3.1Vdc @ 0.62A
  // 60 = 3.75Vdc @ 0.87A
  // 100 = 5.5Vdc
  // 200 = 7.42Vdc @ 2.19A

}

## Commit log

2017-11-13 Added Pictures - Removed Gear-4 sets in wrong direction
    [Alt-LowerMount.skp, Alt-LowerMount.stl, AlternatorModel.skp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]
2017-11-23 New Updates
    [Alt-LowerMount.skp, Alt-LowerMount.stl, Alt-UpperMount.skp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]
2017-11-24 Added Alt-Fan
    [Alt-Fan.skp, Alt-Fan.stl]
2017-12-10 Started Next Version 5-Blades, x20.8152 Gear Ratio. Rail Center pieces and nut holders will not fit until updated.
    [Alt-LowerMount.skp, Alt-LowerMount.stl, Alt-UpperMount.skp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]
2017-12-11 Center pieces updated.
    [Alt-LowerMount.skp, Alt-LowerMount.stl, Alt-UpperMount.skp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]
2018-02-13 Adding Regulator Circuit
    [Alt-LowerMount.skp, Alt-LowerMount.stl, Alt-UpperMount.skp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]
